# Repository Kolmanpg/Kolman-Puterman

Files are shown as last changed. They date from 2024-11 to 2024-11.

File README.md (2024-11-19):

# PCB Design Portfolio

Welcome to my portfolio of PCB design projects! This repository showcases my skills and experience in PCB design, focusing on projects done for my Formula SAE Electric Team, Nittany Motorsports!

## About Me
I am an Electrical Engineering student with a minor in Computer Engineering at Penn State University, experienced in PCB layout, circuit design, and testing. Apart from my work as a project manager for Nittany Motorsports, I am an Undergraduate Research Assistant. My research focuses on power delivery applications in the semiconductor packaging industry.

## Projects

### 1. **Megaboard Front**
- **Description:** This board is responsible for controlling key aspects of the race vehicle. It is built around an STM32F4 and contains various features that allow the vehicle to function as designed and adhere to all regulations.
- **Key Features:**
  - Custom power delivery architecture with multi-stage voltage regulation to ensure maximum efficiency.
  - Integration of high-speed components on the same board as sensitive analog circuits.
  - Integration of multiple safety circuits as required by the rulebook.
- **3D Rendering:**
Megaboard Front V3

### 2. **Megaboard Rear**
- **Description:** This board is responsible for controlling key aspects of the race vehicle. It is built around an STM32F4 and contains various features that allow the vehicle to function as designed and adhere to all regulations.
- **Key Features:**
  - Custom power delivery architecture with multi-stage voltage regulation to ensure maximum efficiency.
  - Integration of high-speed components on the same board as sensitive analog circuits.
  - Integration of both high-voltage and low-voltage circuits on the same board while ensuring necessary isolation.
  - Includes an ESP32 microcontroller utilized for Over-The-Air (OTA) software updates and telemetry.
- **3D Rendering:**
Megaboard Rear V3

### 3. **BMS Segment PCB (ADBMS6830B)**
- **Description:** Developed a Battery Management System (BMS) segment PCB centered around the ADBMS6830B. This PCB is custom-built to fit exactly on top of one of our high-voltage battery segments. It is designed to monitor and discharge all 16 cells on a segment and is built to endure high EMI and noise commonly found inside large high-voltage battery packs.
- **Key Features:**
  - High-precision cell voltage monitoring.
  - Dual isoSPI channels.
  - Stackup configured to minimize noise across the PCB.
- **3D Rendering:**
Segment PCB

## Skills Demonstrated
- Multi-layer PCB layout and design
- Integration of high-speed and high-power components
- Expertise in battery management systems and related ICs
- Prototyping and functional testing

## Repository Structure
Each folder of the repository contains:
- KiCad project files (schematics, layouts, and designs)
- Gerber files for PCB manufacturing
- Bill of Materials (BOM) for component sourcing

## Tools Used
- **PCB Design:** KiCad, Altium Designer
- **Simulations:** LTSPICE, MATLAB, Multisim
- **Prototyping:** Oscilloscopes, Logic Analyzers, Power Supplies, Arbitrary Waveform Generators

## Get in Touch
Feel free to reach out to me with any questions or collaboration ideas!

- Email: Kolmanpg@gmail.com
- [LinkedIn](https://www.linkedin.com/in/Kolmanp)

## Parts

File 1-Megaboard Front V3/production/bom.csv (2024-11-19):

Designator | Footprint | Quantity | Value | LCSC Part #
+VIN1, +VOUT1, -VIN1, -VOUT1, TP1, TP10, TP11, TP12, TP13, TP14, TP15, TP16, TP17, TP18, TP19, TP2, TP20, TP21, TP22, TP23, TP24, TP25, TP26, TP27, TP28, TP29, TP3, TP30, TP31, TP32, TP33, TP34, TP35, TP37, TP38, TP39, TP4, TP41, TP42, TP43, TP44, TP46, TP47, TP5, TP6, TP8, TP9 | TestPoint_Pad_D1.0mm | 47 | ~ | DNP
C1, C10, C11, C12, C22, C23, C25, C27, C29, C3, C30, C31, C33, C37, C4, C41, C46, C49, C5, C50, C51, C6, C7, C8, C9 | 0805 | 25 | 0.1u | C49678
C13, C14 | 0805 | 2 | DNP | DNP
C15, C16, C17, C18, C19, C20, C34, C35, C44, C52, C53, C54 | 0805 | 12 | 1u | C28323
C2 | 0805 | 1 | 4.7u | C1779
C21, C26 | 0805 | 2 | _MHz | DNP
C24, C28 | 0805 | 2 | C_Small | DNP
C32, C48 | 0805 | 2 | 1n | C46653
C36, C47 | 0805 | 2 | 10u | C15850
C38, C39, C42, C43 | CP_EIA-3216-18_Kemet-A | 4 | 10u | C7171
C40 | 0805 | 1 | 10n | C1710
C45 | PCAP_TPB_D4_PAN | 1 | 220u | C242173
D1, D2, D3, D4, D5, D6, D7, D8 | SOD323_F_ | 8 | 1PS76SB17-115 | C551398
D10 | SOT-23 | 1 | NUP2105L | C2890118
D11 | D_SMA | 1 | SS34 | C8678
D12, D13, D16, D9 | 0805 | 4 | NCD0805R1 | C84256
D14 | D_SMA_Handsoldering | 1 | 1N4004 | C727080
D15 | 0805 | 1 | LED | C2297
D17 | HPZRC14X | 1 | HPZR-C14X | DNP
H1, H2, H3, H4 | MountingHole_3.2mm_M3 | 4 | MountingHole | DNP
J1 | PinHeader_2x03_P2.54mm_Vertical | 1 | Conn_01x06 | DNP
J2 | CONN_500762-1001_MOL | 1 | 5007621001 | DNP
JP1 | SolderJumper-2_P1.3mm_Open_RoundedPad1.0x1.5mm | 1 | NC | DNP
JP2, JP3, JP4 | SolderJumper-3_P1.3mm_Open_RoundedPad1.0x1.5mm | 3 | SolderJumper_3_Open
K1 | RELAY_DSP2A_PAN | 1 | DSP2A-DC12V | DNP
L1 | IND_CDRH104_SUM | 1 | 15uH | C225048
Q1, Q2, Q3 | SOT-23 | 3 | MMBF170 | C151058
Q4 | SOT-23 | 1 | MMFTP2319 | DNP
R1 | 0805 | 1 | 2k2 | C17520
R10, R3, R36, R4, R42, R48, R49, R50, R55, R57, R61, R65, R66, R68, R69, R7, R8, R85, R86, R9 | 0805 | 20 | 10k | C17414
R11, R12, R15, R16, R17, R18, R64 | 0805 | 7 | 3k8 | C228799
R13, R14, R46, R47, R82, R84 | 0805 | 6 | 9.7k | C374689
R19, R53 | 0805 | 2 | 200 | C17540
R2, R59, R60, R71, R87 | 0805 | 5 | 100k | C149504
R20, R21, R28 | 0805 | 3 | 0R | C17477
R22, R23, R24, R25, R26, R27 | 0805 | 6 | 82 | C17841
R29, R41, R56 | 0805 | 3 | 15k | C17475
R30 | 0805 | 1 | 66
R31 | 0805 | 1 | 14k | C17464
R32 | 0805 | 1 | 453
R33 | 0805 | 1 | 120 | C17437
R34, R35 | 0805 | 2 | 1M | C17514
R37, R38, R51, R77 | 0805 | 4 | 82k | C17840
R39, R40, R52, R78 | 0805 | 4 | 18k | C17506
R43, R58 | 0805 | 2 | 47k | C17713
R44, R45, R5, R6, R79, R83 | 0805 | 6 | 5k | C2828700
R54 | 0805 | 1 | 68k | C17801
R62 | 0805 | 1 | 3.24k | C4194377
R63 | 0805 | 1 | 330R | C17630
R67 | 0805 | 1 | 2k | C17604
R70, R73, R74 | 0805 | 3 | 1k | C17513
R72 | 0805 | 1 | 300 | C17617
R75, R76, R80, R81 | 0805 | 4 | DNP | C865361
RV1, RV2 | Potentiometer_Bourns_3296W_Vertical | 2 | 1k
RV3, RV4 | Potentiometer_Bourns_3296W_Vertical | 2 | 100k
SW1, SW2 | SW_Push_1P1T_XKB_TS-1187A | 2 | SW_MEC_5G | C318884
U1 | LQFP-64_10x10mm_P0.5mm | 1 | STM32F446RETx | C69336
U10 | TI_SO-PowerPAD-8_ThermalVias | 1 | TPS5431DDA | C9864
U11 | SOIC-14_3.9x8.7mm_P1.27mm | 1 | 74HC14 | C5605
U12, U13, U14, U17 | SOIC-8_3.9x4.9mm_P1.27mm | 4 | LM393 | C32901
U15 | SOT95P280X125-5N | 1 | BU4S71G2-TR | C2837802
U16 | SOIC127P600X175-14N | 1 | HEF4081BT,653 | C148318
U2, U3, U4, U5, U8 | SOIC-8_3.9x4.9mm_P1.27mm | 5 | LM358 | C9418
U6 | SOIC-16_3.9x9.9mm_P1.27mm | 1 | MAX3232 | C18261
U7 | SOIC-8_3.9x4.9mm_P1.27mm | 1 | SN65HVD230 | C12084
U9 | SOT-223-3_TabPin2 | 1 | AMS1117-3.3 | C6186
Y1 | Crystal_SMD_3225-4Pin_3.2x2.5mm_HandSoldering | 1 | Crystal_GND24_Small
Y2 | Crystal_SMD_3215-2Pin_3.2x1.5mm | 1 | Crystal_GND23_Small | DNP

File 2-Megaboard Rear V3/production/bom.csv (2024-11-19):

Designator | Footprint | Quantity | Value | LCSC Part #
C1, C10, C11, C12, C13, C14, C15, C16, C17, C2, C20, C25, C26, C28, C3, C30, C31, C38, C4, C43, C6, C7, C8, C9 | 0805 | 24 | 0.1u | C28233
C18, C19, C36, C37, C39, C40, C46, C47 | CP_EIA-3216-18_Kemet-A | 8 | 10u | C7171
C21, C22 | 0805 | 2 | 20p | C1798
C23, C24 | 0805 | 2 | 22p | C1804
C27, C29 | 0805 | 2 | 2.2n | C28260
C32, C35 | 0805 | 2 | 1u | DNP
C33, C49 | 0805 | 2 | 10n | C1710
C34, C48 | 0805 | 2 | 10u | C15850
C41, C42, C44, C45, C51 | 0805 | 5 | 1u | C28323
C5 | 0805 | 1 | 4.7u | C1779
C50 | PCAP_TPB_D4_PAN | 1 | 220u | C242173
C52 | 0805 | 1 | DNP | DNP
D1, D13 | SOT-23 | 2 | NUP2105L | C284104
D10, D11, D12, D6, D7, D9 | D_MiniMELF | 6 | ZMM3V3-M | DNP
D14, D15, D16, D17, D19, D2, D4 | 0805 | 7 | NCD0805R1 | C84256
D18 | D_SMA | 1 | SS34 | C8678
D3 | D_SMA | 1 | US1M | C412437
D5 | D_MiniMELF | 1 | BZV55C15 | C545332
D8 | 0805 | 1 | KT-0805G | C2297
H1, H2, H3, H4 | MountingHole_3.2mm_M3 | 4 | MountingHole | DNP
HV+1, HV-1, TP1, TP36, TP37 | TestPoint_Pad_D1.0mm | 5 | HIL_TSAL_HV_GND | DNP
J1 | CONN_500762-1001_MOL | 1 | 5007621001 | DNP
J2 | microSD_HC_Molex_104031-0811 | 1 | Micro_SD_Card_Det | C585350
J3 | PinHeader_1x03_P2.54mm_Vertical | 1 | Conn_01x03
J4 | PinHeader_2x03_P2.54mm_Vertical | 1 | Conn_02x03_Odd_Even
J5 | PinHeader_1x04_P2.54mm_Vertical | 1 | Conn_01x04 | DNP
JP1, JP2 | SolderJumper-2_P1.3mm_Open_RoundedPad1.0x1.5mm | 2 | NC | DNP
JP5, JP6 | SolderJumper-2_P1.3mm_Open_RoundedPad1.0x1.5mm | 2 | Jumper_2_Open
L1 | IND_CDRH104_SUM | 1 | 15uH | C225048
Q1, Q2, Q3, Q4 | SOT-23 | 4 | AO3400A | C20917
Q5, Q6, Q7, Q8, Q9 | SOT-23 | 5 | MMBF170 | C20917
R1, R10, R15, R16, R3, R35, R42, R44, R6, R63, R65, R67 | 0805 | 12 | 10k | C17414
R11, R20, R7, R8 | 0805 | 4 | 0R | C17477
R12, R5 | 0805 | 2 | 120 | C17437
R13, R17, R62, R9 | 0805 | 4 | 200 | C17540
R14, R25, R43 | 0805 | 3 | 2k2 | C17520
R18, R19 | 0805 | 2 | 4k7 | C17673
R2, R4 | 0805 | 2 | 4.7k | C17673
R21, R22, R23, R24, R27, R28, R29, R30 | 0805 | 8 | 300k | C149504
R26, R32 | 0805 | 2 | 1k | C17513
R31 | 0805 | 1 | 18k | C17506
R33 | 2512 | 1 | 0.01R | C149504
R34 | 0805 | 1 | 1k2 | C17379
R36, R45, R52, R55, R58, R61 | 0805 | 6 | 9k1 | C17855
R37 | 0805 | 1 | 22k | C17560
R38 | 0805 | 1 | 51k | C17737
R40, R46 | 0805 | 2 | 82 | C17477
R41, R47, R49, R54, R57, R60 | 0805 | 6 | 3k6 | C18359
R48 | 0805 | 1 | 1k3 | C17414
R50, R53, R56, R59 | 0805 | 4 | 82 | C23255
R51 | 0805 | 1 | 47 | C17714
R64 | 0805 | 1 | 3.24k | C4194377
R66 | 0805 | 1 | 330R | C17630
SW1, SW2, SW3, SW4 | SW_Push_1P1T_XKB_TS-1187A | 4 | SW_MEC_5G | C318884
TP10, TP11, TP12, TP13, TP14, TP15, TP16, TP17, TP18, TP19, TP20, TP21, TP22, TP23, TP24, TP25, TP26, TP27, TP28, TP29, TP30, TP31, TP32, TP33, TP34, TP35, TP38, TP39, TP40, TP5, TP6, TP7, TP8, TP9 | TestPoint_Pad_D1.0mm | 34 | ~ | DNP
TP2 | TestPoint_Pad_D1.0mm | 1 | HIL_IN_TSAL | DNP
TP3 | TestPoint_Pad_D1.0mm | 1 | DIS | DNP
TP4 | TestPoint_Pad_D1.0mm | 1 | THR | DNP
U1, U5 | SOIC-8_3.9x4.9mm_P1.27mm | 2 | SN65HVD230 | C12084
U10, U15, U17 | SOIC-8_3.9x4.9mm_P1.27mm | 3 | LM358 | C7950
U11 | SOIC-8_3.9x4.9mm_P1.27mm | 1 | NE555DR | C7593
U12 | SOP-4_3.8x4.1mm_P2.54mm | 1 | EL357NC | C29981
U13 | D24V150F12 | 1 | DV24V150F12 | DNP
U14, U16 | SOT-223-3_TabPin2 | 2 | AMS1117-3.3
U18 | TI_SO-PowerPAD-8_ThermalVias | 1 | TPS5431DDA
U2 | SOT-23-6 | 1 | TMP101 | C388175
U3 | ESP32-WROOM-32 | 1 | ESP32-WROOM-32 | C529581
U4 | LQFP-64_10x10mm_P0.5mm | 1 | STM32F446RETx | C69336
U6 | TSSOP-16_4.4x5mm_P0.65mm | 1 | MAX3232 | C13482
U7 | Converter_DCDC_TRACO_TMR-xxxx_THT | 1 | TMR-1212 | DNP
U8 | InvenSense_QFN-24_4x4mm_P0.5mm | 1 | MPU-6050 | C24112
U9 | SOIC-8_3.9x4.9mm_P1.27mm | 1 | LM393 | C7955
Y1 | Crystal_SMD_3225-4Pin_3.2x2.5mm_HandSoldering | 1 | 9p | C13738
Y2 | Crystal_SMD_3215-2Pin_3.2x1.5mm | 1 | 12p5 | C32346

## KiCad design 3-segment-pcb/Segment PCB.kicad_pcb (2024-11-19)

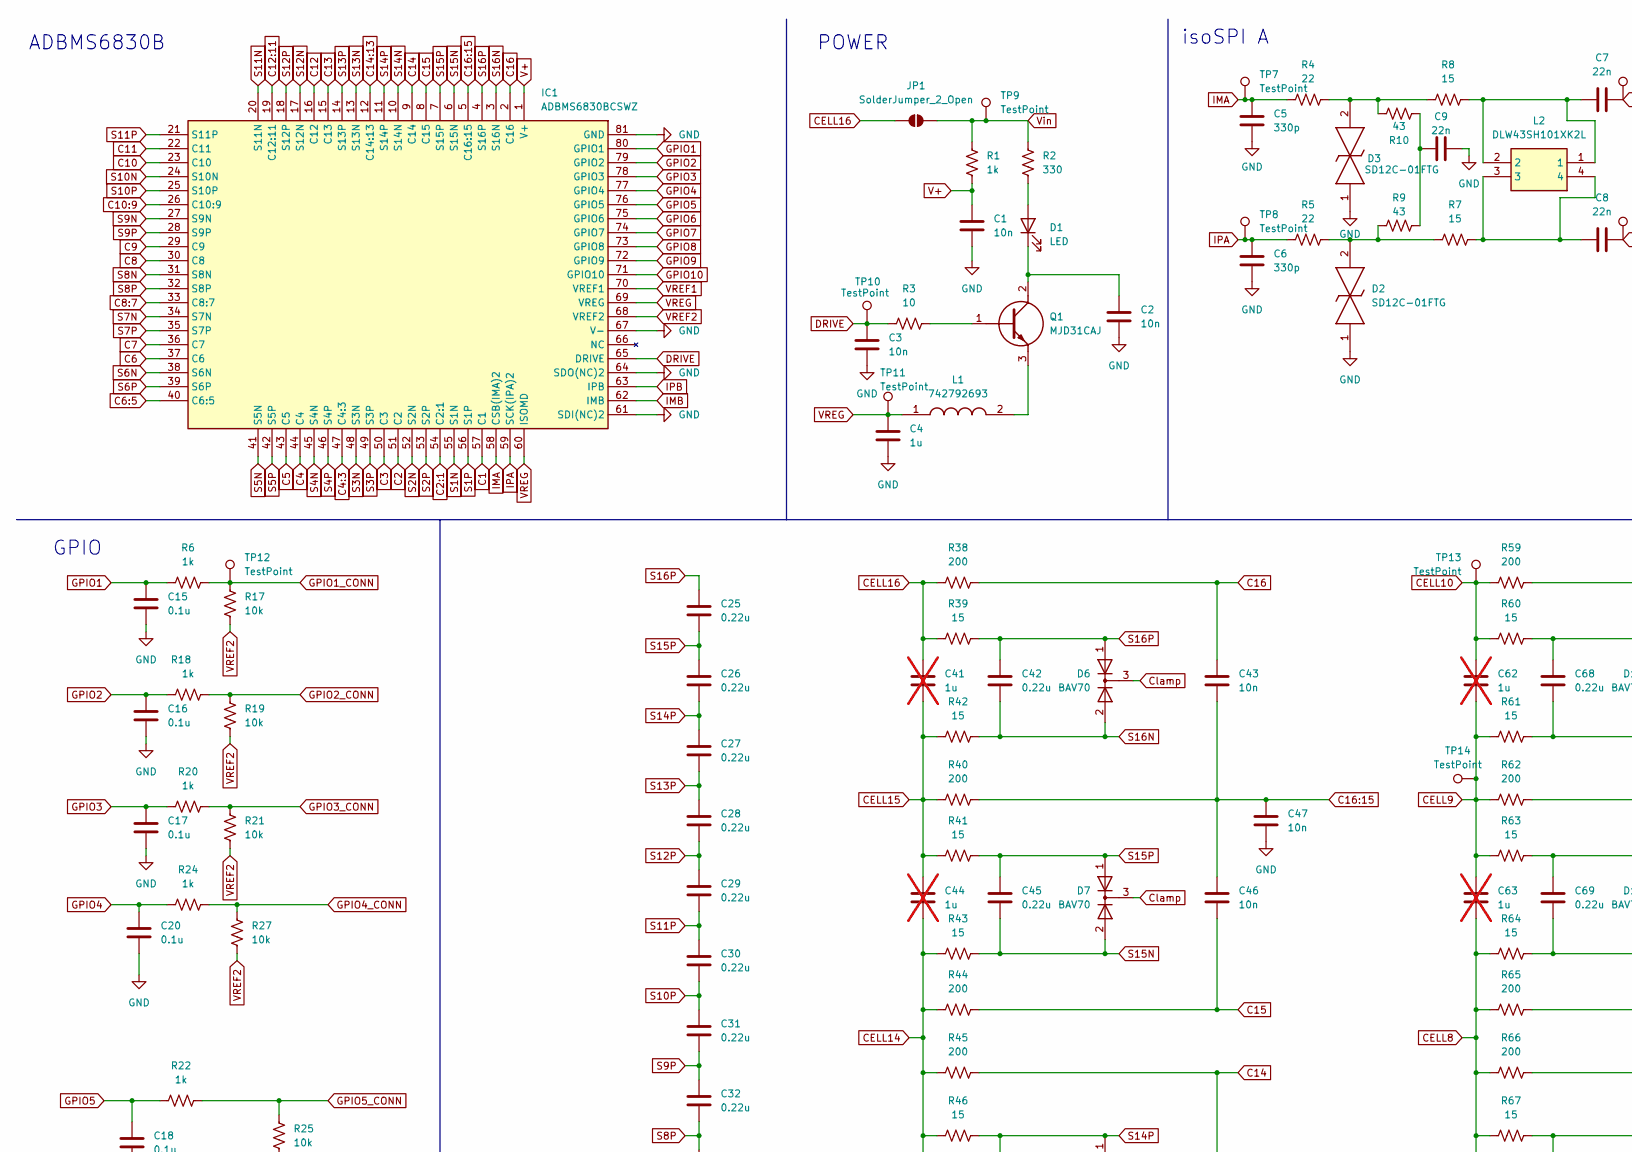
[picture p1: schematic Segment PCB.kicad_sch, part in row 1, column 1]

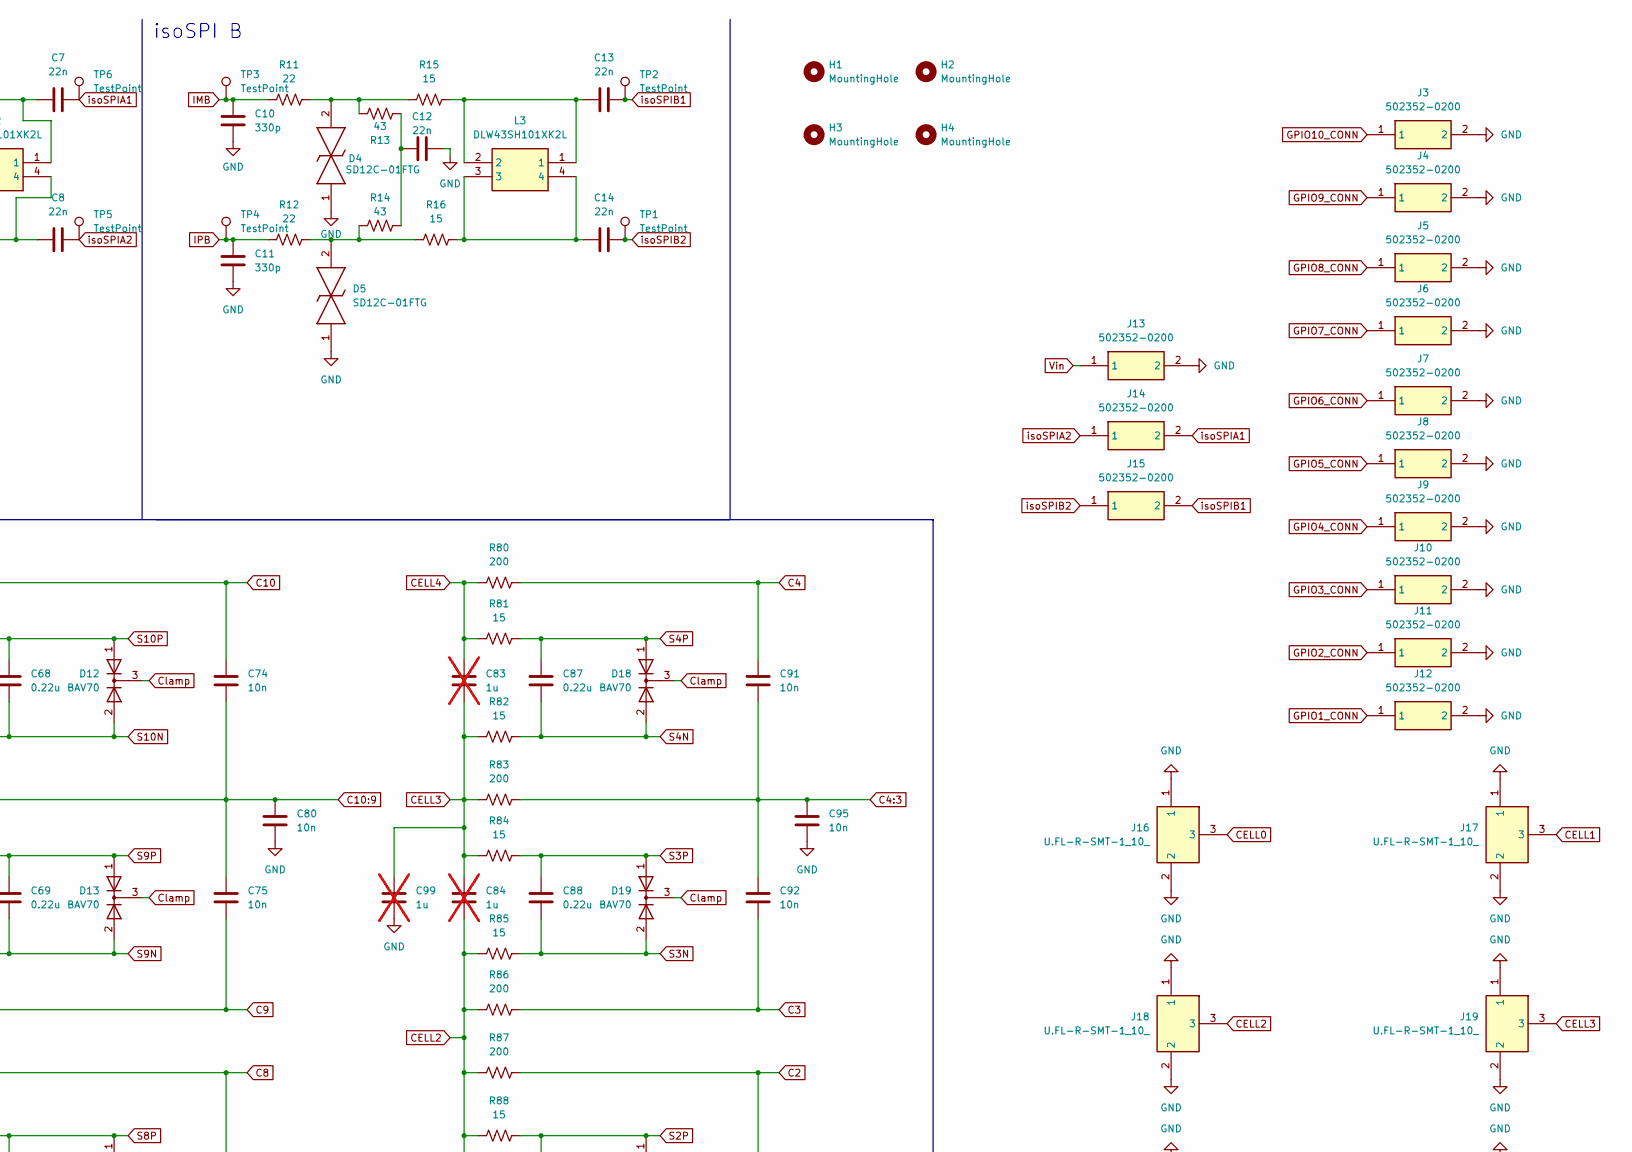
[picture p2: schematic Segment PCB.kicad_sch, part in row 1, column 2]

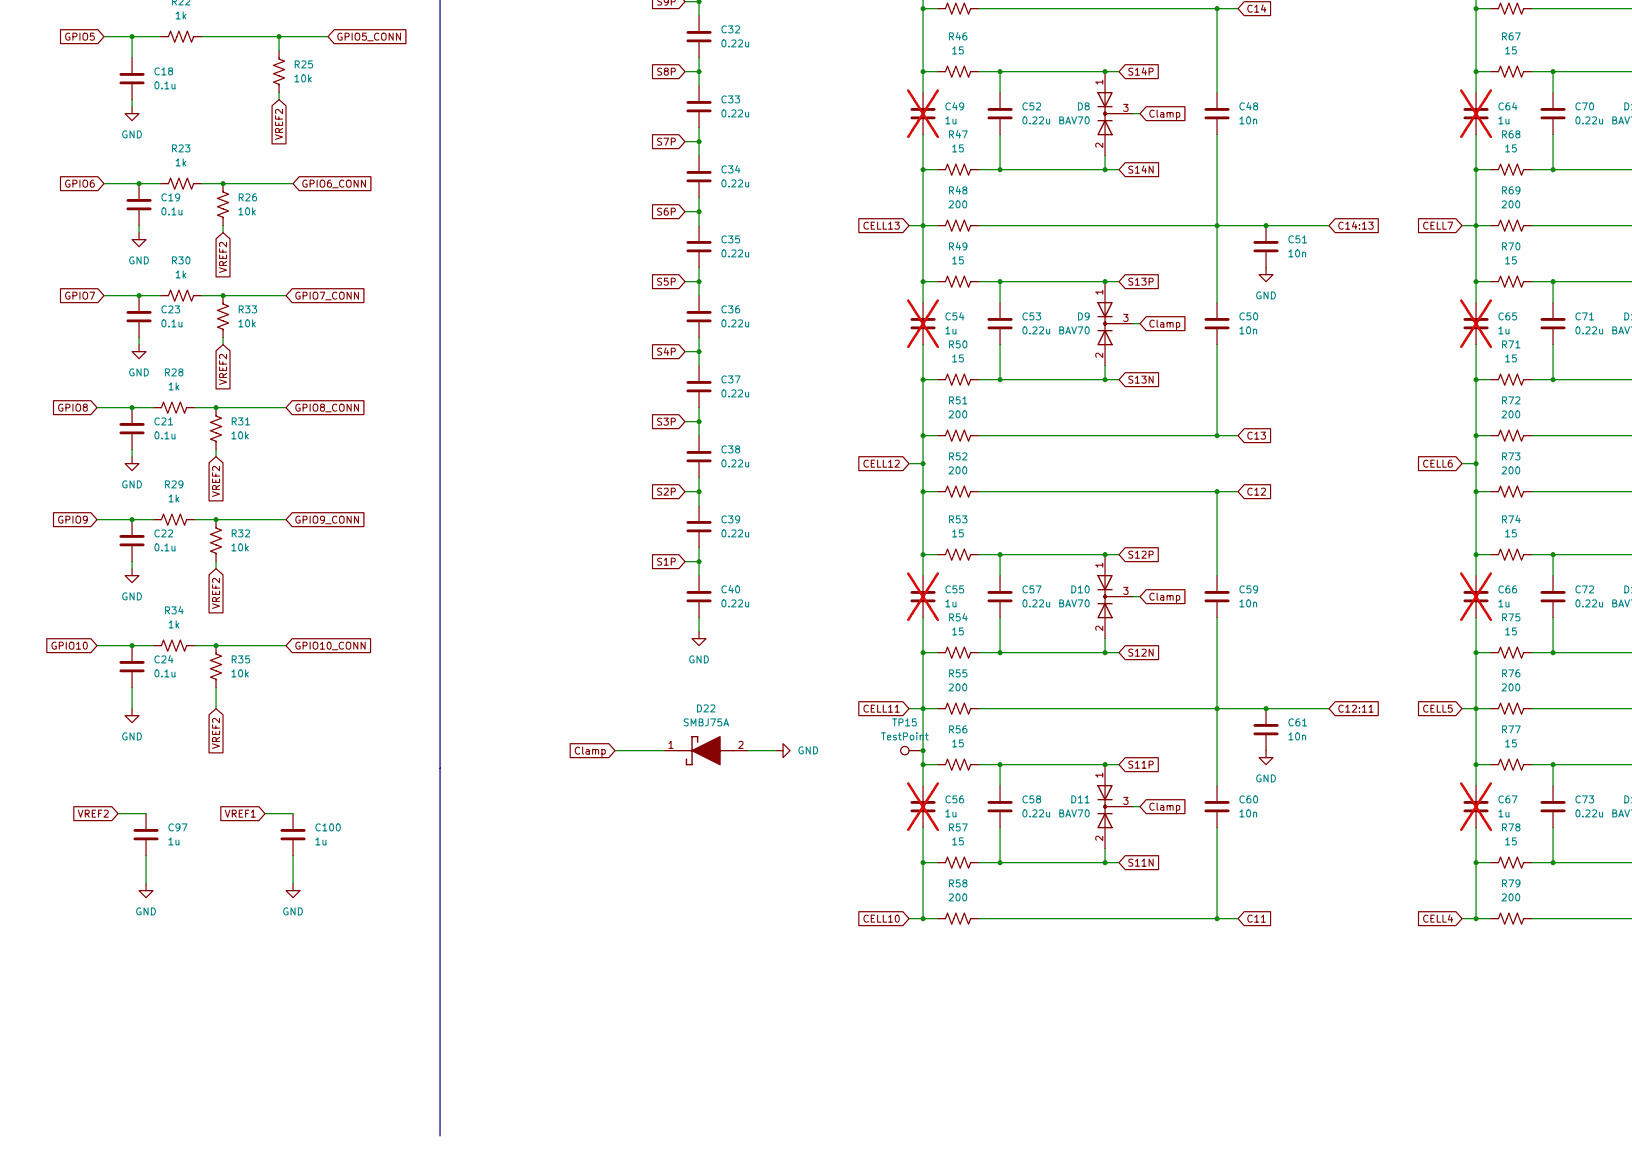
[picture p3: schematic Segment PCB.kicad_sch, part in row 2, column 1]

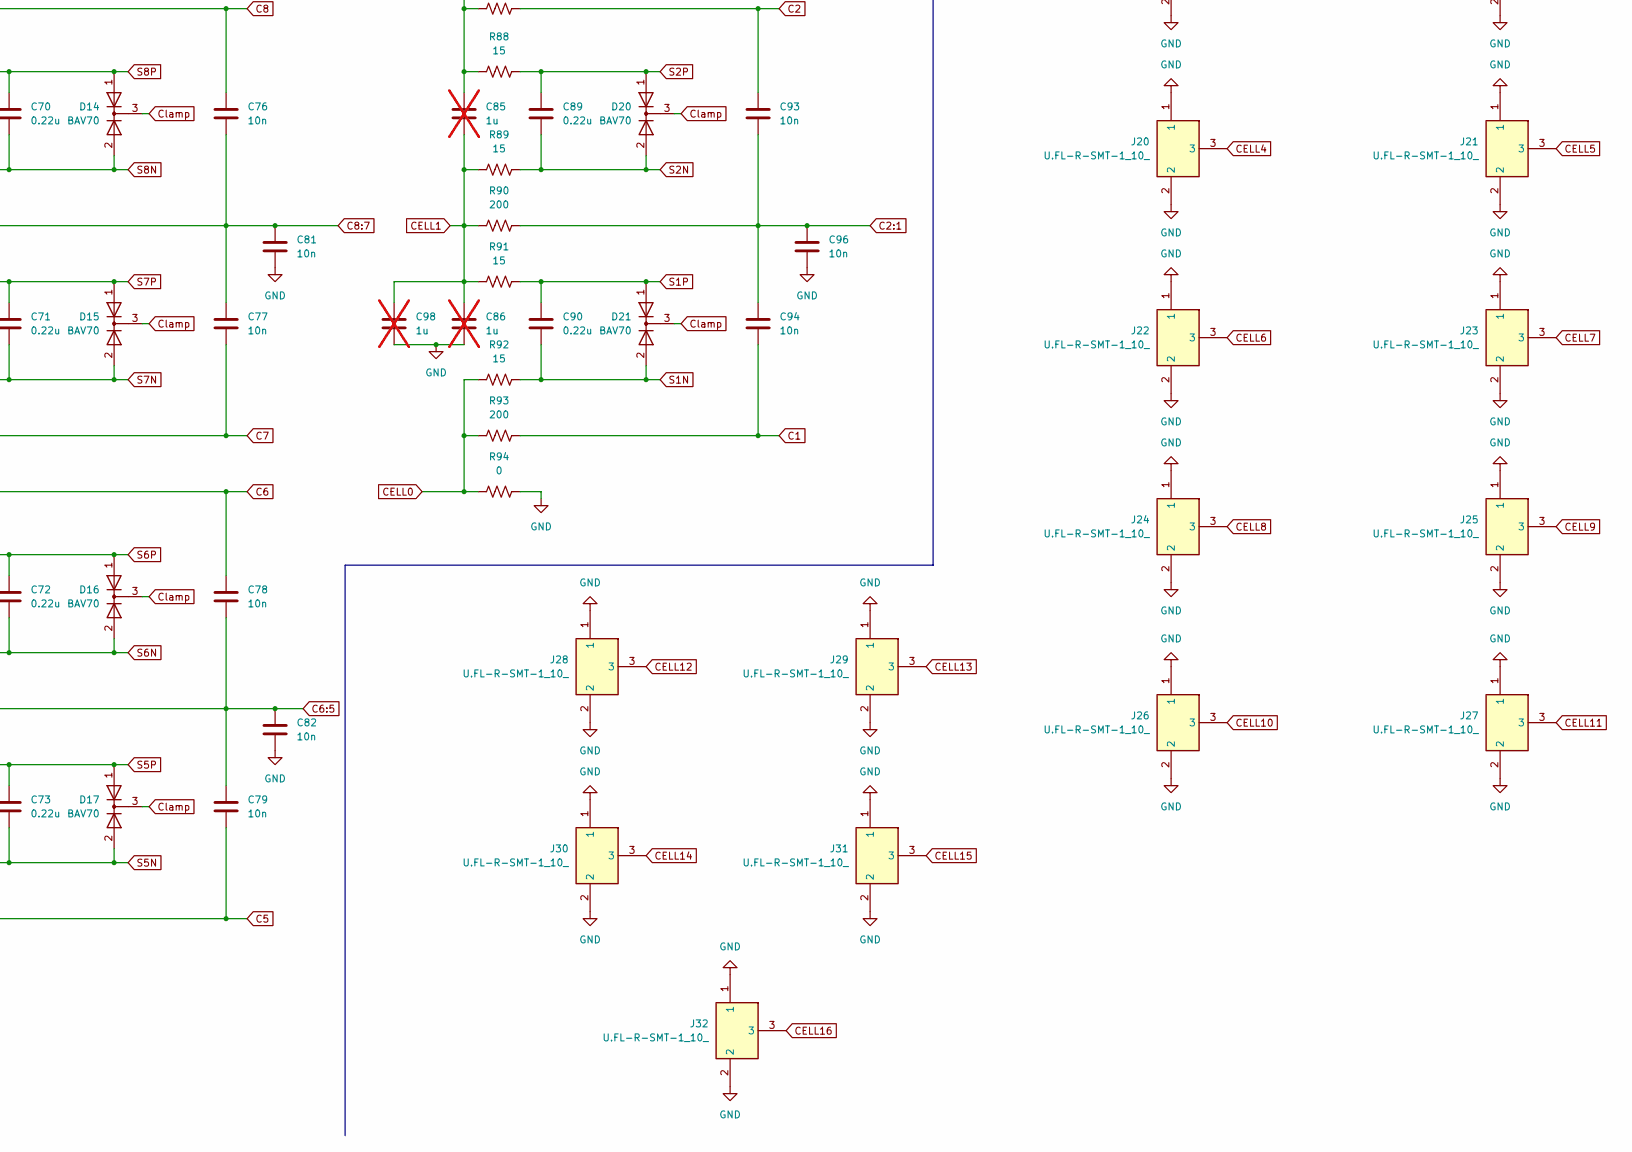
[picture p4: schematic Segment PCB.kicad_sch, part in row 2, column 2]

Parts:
C1, C2, C3, C43, C46, C47, C48, C50, C51, C59, C60, C61, C74, C75, C76, C77, C78, C79, C80, C81, C82, C91, C92, C93, C94, C95, C96: 10n; C_0805_2012Metric_Pad1.18x1.45mm_HandSolder; Manufacturer_Part_Number CL21B103KBANNNC; JLCPCB C1710
C4, C97, C100: 1u; C_0805_2012Metric_Pad1.18x1.45mm_HandSolder; Manufacturer_Part_Number CL21B105KBFNNNE; JLCPCB C28323
C5, C6, C10, C11: 330p; C_0805_2012Metric_Pad1.18x1.45mm_HandSolder
C7, C8, C9, C12, C13, C14: 22n; C_0805_2012Metric_Pad1.18x1.45mm_HandSolder; Manufacturer_Part_Number CL21B223KBANNNC; JLCPCB C1729
C15, C16, C17, C18, C19, C20, C21, C22, C23, C24: 0.1u; C_0805_2012Metric_Pad1.18x1.45mm_HandSolder; Manufacturer_Part_Number CL21B104KCFNNNE; JLCPCB C28233
C25, C26, C27, C28, C29, C30, C31, C32, C33, C34, C35, C36, C37, C38, C39, C40, C42, C45, C52, C53, C57, C58, C68, C69, C70, C71, C72, C73, C87, C88, C89, C90: 0.22u; C_0805_2012Metric_Pad1.18x1.45mm_HandSolder; Manufacturer_Part_Number CL21B224KBFNNNE; JLCPCB C5378
C41, C44, C49, C54, C55, C56, C62, C63, C64, C65, C66, C67, C83, C84, C85, C86, C98, C99: 1u; C_0805_2012Metric_Pad1.18x1.45mm_HandSolder; Manufacturer_Part_Number CL21B105KBFNNNE; JLCPCB C28323; not fitted
D1: LED; LED_0805_2012Metric_Pad1.15x1.40mm_HandSolder; Manufacturer_Part_Number KT-0805G; JLCPCB C2297
D2, D3, D4, D5: SD12C-01FTG; SOD2613X114N; Mouser Part Number 576-SD12C-01FTG
D6, D7, D8, D9, D10, D11, D12, D13, D14, D15, D16, D17, D18, D19, D20, D21: BAV70; SOT-23; Manufacturer_Part_Number BAV70; JLCPCB C68978
D22: SMBJ75A; Mouser Part Number 750-CDBB3200-HF
H1, H2, H3, H4: MountingHole; MountingHole_3mm
IC1: ADBMS6830BCSWZ; QFP50P1400X1400X160-81N; Mouser Part Number 584-ADBMS6830BCSWZ
J3, J4, J5, J6, J7, J8, J9, J10, J11, J12, J13, J14, J15: 502352-0200; 5023520200; Mouser Part Number 538-502352-0200
J16, J17, J18, J19, J20, J21, J22, J23, J24, J25, J26, J27, J28, J29, J30, J31, J32: U.FL-R-SMT-1_10_; Mouser Part Number 798-U.FL-R-SMT-110
JP1: SolderJumper_2_Open; SolderJumper-2_P1.3mm_Open_RoundedPad1.0x1.5mm
L1: 742792693; INDC1608X100N; Mouser Part Number 710-742792693
L2, L3: DLW43SH101XK2L; Mouser Part Number 81-DLW43SH101XK2L
Q1: MJD31CAJ; Mouser Part Number 771-MJD31CAJ
R1, R6, R18, R20, R22, R23, R24, R28, R29, R30, R34: 1k; R_0805_2012Metric_Pad1.20x1.40mm_HandSolder; Manufacturer_Part_Number 0805W8F1001T5E; JLCPCB C17513
R2: 330; R_0805_2012Metric_Pad1.20x1.40mm_HandSolder; Manufacturer_Part_Number 0805W8F3300T5E; JLCPCB C17630
R3: 10; R_0805_2012Metric_Pad1.20x1.40mm_HandSolder; Manufacturer_Part_Number 0805W8F100JT5E; JLCPCB C17415
R4, R5, R11, R12: 22; R_0805_2012Metric_Pad1.20x1.40mm_HandSolder; Manufacturer_Part_Number 0805W8F220JT5E; JLCPCB C17561
R7, R8, R15, R16: 15; R_0805_2012Metric_Pad1.20x1.40mm_HandSolder
R9, R10, R13, R14: 43; R_0805_2012Metric_Pad1.20x1.40mm_HandSolder
R17, R19, R21, R25, R26, R27, R31, R32, R33, R35: 10k; R_0805_2012Metric_Pad1.20x1.40mm_HandSolder; Manufacturer_Part_Number 0805W8F1002T5E; JLCPCB C17414
R38, R40, R44, R45, R48, R51, R52, R55, R58, R59, R62, R65, R66, R69, R72, R73, R76, R79, R80, R83, R86, R87, R90, R93: 200; R_0805_2012Metric_Pad1.20x1.40mm_HandSolder; Manufacturer_Part_Number 0805W8F2000T5E; JLCPCB C17540
R39, R41, R42, R43, R46, R47, R49, R50, R53, R54, R56, R57, R60, R61, R63, R64, R67, R68, R70, R71, R74, R75, R77, R78, R81, R82, R84, R85, R88, R89, R91, R92: 15; RESC6432X65N; Manufacturer_Part_Number 352115RFT
R94: 0; R_0805_2012Metric_Pad1.20x1.40mm_HandSolder; Manufacturer_Part_Number 0805W8F0000T5E; JLCPCB C17477
TP1, TP2, TP3, TP4, TP5, TP6, TP7, TP8, TP9, TP10, TP11, TP12, TP13, TP14, TP15: TestPoint; TestPoint_Pad_D1.0mm

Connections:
C1: C94.2, IC1.57 (C1), R93.2
C2: C93.1, IC1.51 (C2), R87.2
C2:1: C93.2, C94.1, C96.1, IC1.54 (C2:1), R90.2
C3: C92.2, IC1.50 (C3), R86.2
C4: C91.1, IC1.44 (C4), R80.2
C4:3: C91.2, C92.1, C95.1, IC1.47 (C4:3), R83.2
C5: C79.2, IC1.43 (C5), R79.2
C6: C78.1, IC1.37 (C6), R73.2
C6:5: C78.2, C79.1, C82.1, IC1.40 (C6:5), R76.2
C7: C77.2, IC1.36 (C7), R72.2
C8: C76.1, IC1.30 (C8), R66.2
C8:7: C76.2, C77.1, C81.1, IC1.33 (C8:7), R69.2
C9: C75.2, IC1.29 (C9), R65.2
C10: C74.1, IC1.23 (C10), R59.2
C10:9: C74.2, C75.1, C80.1, IC1.26 (C10:9), R62.2
C11: C60.2, IC1.22 (C11), R58.2
C12: C59.1, IC1.16 (C12), R52.2
C12:11: C59.2, C60.1, C61.1, IC1.19 (C12:11), R55.2
C13: C50.2, IC1.15 (C13), R51.2
C14: C48.1, IC1.9 (C14), R45.2
C14:13: C48.2, C50.1, C51.1, IC1.12 (C14:13), R48.2
C15: C46.2, IC1.8 (C15), R44.2
C16: C43.1, IC1.2 (C16), R38.2
C16:15: C43.2, C46.1, C47.1, IC1.5 (C16:15), R40.2
CELL0: J16.3, R92.1, R93.1, R94.1
CELL1: C85.2, C86.1, C98.1, J17.3, R89.1, R90.1, R91.1
CELL2: C84.2, C85.1, J18.3, R85.1, R86.1, R87.1, R88.1
CELL3: C83.2, C84.1, C99.1, J19.3, R82.1, R83.1, R84.1
CELL4: C67.2, C83.1, J20.3, R78.1, R79.1, R80.1, R81.1
CELL5: C66.2, C67.1, J21.3, R75.1, R76.1, R77.1
CELL6: C65.2, C66.1, J22.3, R71.1, R72.1, R73.1, R74.1
CELL7: C64.2, C65.1, J23.3, R68.1, R69.1, R70.1
CELL8: C63.2, C64.1, J24.3, R64.1, R65.1, R66.1, R67.1
CELL9: C62.2, C63.1, J25.3, R61.1, R62.1, R63.1, TP14.1
CELL10: C56.2, C62.1, J26.3, R57.1, R58.1, R59.1, R60.1, TP13.1
CELL11: C55.2, C56.1, J27.3, R54.1, R55.1, R56.1, TP15.1
CELL12: C54.2, C55.1, J28.3, R50.1, R51.1, R52.1, R53.1
CELL13: C49.2, C54.1, J29.3, R47.1, R48.1, R49.1
CELL14: C44.2, C49.1, J30.3, R43.1, R44.1, R45.1, R46.1
CELL15: C41.2, C44.1, J31.3, R40.1, R41.1, R42.1
CELL16: C41.1, J32.3, JP1.1 (A), R38.1, R39.1
Clamp: D6.3 (K), D7.3 (K), D8.3 (K), D9.3 (K), D10.3 (K), D11.3 (K), D12.3 (K), D13.3 (K), D14.3 (K), D15.3 (K), D16.3 (K), D17.3 (K), D18.3 (K), D19.3 (K), D20.3 (K), D21.3 (K), D22.1 (K)
DRIVE: C3.1, IC1.65 (DRIVE), R3.1, TP10.1
GND: C1.2, C2.2, C3.2, C4.2, C5.2, C6.2, C9.2, C10.2, C11.2, C12.2, C15.2, C16.2, C17.2, C18.2, C19.2, C20.2, C21.2, C22.2, C23.2, C24.2, C40.2, C47.2, C51.2, C61.2, C80.2, C81.2, C82.2, C86.2, C95.2, C96.2, C97.2, C98.2, C99.2, C100.2, D2.1, D3.1, D4.1, D5.1, D22.2 (A), IC1.61 (SDI(NC)2), IC1.64 (SDO(NC)2), IC1.67 (V-), IC1.81 (GND), J3.2, J4.2, J5.2, J6.2, J7.2, J8.2, J9.2, J10.2, J11.2, J12.2, J13.2, J16.1, J16.2, J17.1, J17.2, J18.1, J18.2, J19.1, J19.2, J20.1, J20.2, J21.1, J21.2, J22.1, J22.2, J23.1, J23.2, J24.1, J24.2, J25.1, J25.2, J26.1, J26.2, J27.1, J27.2, J28.1, J28.2, J29.1, J29.2, J30.1, J30.2, J31.1, J31.2, J32.1, J32.2, R94.2
GPIO1: C15.1, IC1.80 (GPIO1), R6.1
GPIO1_CONN: J12.1, R6.2, R17.2, TP12.1
GPIO2: C16.1, IC1.79 (GPIO2), R18.1
GPIO2_CONN: J11.1, R18.2, R19.2
GPIO3: C17.1, IC1.78 (GPIO3), R20.1
GPIO3_CONN: J10.1, R20.2, R21.2
GPIO4: C20.1, IC1.77 (GPIO4), R24.1
GPIO4_CONN: J9.1, R24.2, R27.2
GPIO5: C18.1, IC1.76 (GPIO5), R22.1
GPIO5_CONN: J8.1, R22.2, R25.2
GPIO6: C19.1, IC1.75 (GPIO6), R23.1
GPIO6_CONN: J7.1, R23.2, R26.2
GPIO7: C23.1, IC1.74 (GPIO7), R30.1
GPIO7_CONN: J6.1, R30.2, R33.2
GPIO8: C21.1, IC1.73 (GPIO8), R28.1
GPIO8_CONN: J5.1, R28.2, R31.2
GPIO9: C22.1, IC1.72 (GPIO9), R29.1
GPIO9_CONN: J4.1, R29.2, R32.2
GPIO10: C24.1, IC1.71 (GPIO10), R34.1
GPIO10_CONN: J3.1, R34.2, R35.2
IMA: C5.1, IC1.58 (CSB(IMA)2), R4.1, TP7.1
IMB: C10.1, IC1.62 (IMB), R11.1, TP3.1
IPA: C6.1, IC1.59 (SCK(IPA)2), R5.1, TP8.1
IPB: C11.1, IC1.63 (IPB), R12.1, TP4.1
unnamed: C7.1, L2.1, L2.2, R8.2
unnamed: C8.1, L2.3, L2.4, R7.2
unnamed: C9.1, R9.2, R10.1
unnamed: C12.1, R13.1, R14.2
unnamed: C13.1, L3.1, L3.2, R15.2
unnamed: C14.1, L3.3, L3.4, R16.2
unnamed: D1.2 (A), R2.2
unnamed: C2.1, D1.1 (K), Q1.2 (C)
unnamed: D2.2, R5.2, R7.1, R9.1
unnamed: D3.2, R4.2, R8.1, R10.2
unnamed: D4.2, R11.2, R13.2, R15.1
unnamed: D5.2, R12.2, R14.1, R16.1
unnamed: Q1.1 (B), R3.2
unnamed: L1.2, Q1.3 (E)
S1N: C90.2, D21.2 (A), IC1.55 (S1N), R92.2
S1P: C39.2, C40.1, C90.1, D21.1 (A), IC1.56 (S1P), R91.2
S2N: C89.2, D20.2 (A), IC1.52 (S2N), R89.2
S2P: C38.2, C39.1, C89.1, D20.1 (A), IC1.53 (S2P), R88.2
S3N: C88.2, D19.2 (A), IC1.48 (S3N), R85.2
S3P: C37.2, C38.1, C88.1, D19.1 (A), IC1.49 (S3P), R84.2
S4N: C87.2, D18.2 (A), IC1.45 (S4N), R82.2
S4P: C36.2, C37.1, C87.1, D18.1 (A), IC1.46 (S4P), R81.2
S5N: C73.2, D17.2 (A), IC1.41 (S5N), R78.2
S5P: C35.2, C36.1, C73.1, D17.1 (A), IC1.42 (S5P), R77.2
S6N: C72.2, D16.2 (A), IC1.38 (S6N), R75.2
S6P: C34.2, C35.1, C72.1, D16.1 (A), IC1.39 (S6P), R74.2
S7N: C71.2, D15.2 (A), IC1.34 (S7N), R71.2
S7P: C33.2, C34.1, C71.1, D15.1 (A), IC1.35 (S7P), R70.2
S8N: C70.2, D14.2 (A), IC1.31 (S8N), R68.2
S8P: C32.2, C33.1, C70.1, D14.1 (A), IC1.32 (S8P), R67.2
S9N: C69.2, D13.2 (A), IC1.27 (S9N), R64.2
S9P: C31.2, C32.1, C69.1, D13.1 (A), IC1.28 (S9P), R63.2
S10N: C68.2, D12.2 (A), IC1.24 (S10N), R61.2
S10P: C30.2, C31.1, C68.1, D12.1 (A), IC1.25 (S10P), R60.2
S11N: C58.2, D11.2 (A), IC1.20 (S11N), R57.2
S11P: C29.2, C30.1, C58.1, D11.1 (A), IC1.21 (S11P), R56.2
S12N: C57.2, D10.2 (A), IC1.17 (S12N), R54.2
S12P: C28.2, C29.1, C57.1, D10.1 (A), IC1.18 (S12P), R53.2
S13N: C53.2, D9.2 (A), IC1.13 (S13N), R50.2
S13P: C27.2, C28.1, C53.1, D9.1 (A), IC1.14 (S13P), R49.2
S14N: C52.2, D8.2 (A), IC1.10 (S14N), R47.2
S14P: C26.2, C27.1, C52.1, D8.1 (A), IC1.11 (S14P), R46.2
S15N: C45.2, D7.2 (A), IC1.6 (S15N), R43.2
S15P: C25.2, C26.1, C45.1, D7.1 (A), IC1.7 (S15P), R41.2
S16N: C42.2, D6.2 (A), IC1.3 (S16N), R42.2
S16P: C25.1, C42.1, D6.1 (A), IC1.4 (S16P), R39.2
V+: C1.1, IC1.1 (V+), R1.2
VREF1: C100.1, IC1.70 (VREF1)
VREF2: C97.1, IC1.68 (VREF2), R17.1, R19.1, R21.1, R25.1, R26.1, R27.1, R31.1, R32.1, R33.1, R35.1
VREG: C4.1, IC1.60 (ISOMD), IC1.69 (VREG), L1.1, TP11.1
Vin: J13.1, JP1.2 (B), R1.1, R2.1, TP9.1
isoSPIA1: C7.2, J14.2, TP6.1
isoSPIA2: C8.2, J14.1, TP5.1
isoSPIB1: C13.2, J15.2, TP2.1
isoSPIB2: C14.2, J15.1, TP1.1

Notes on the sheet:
POWER
isoSPI A
ADBMS6830B
GPIO
isoSPI B

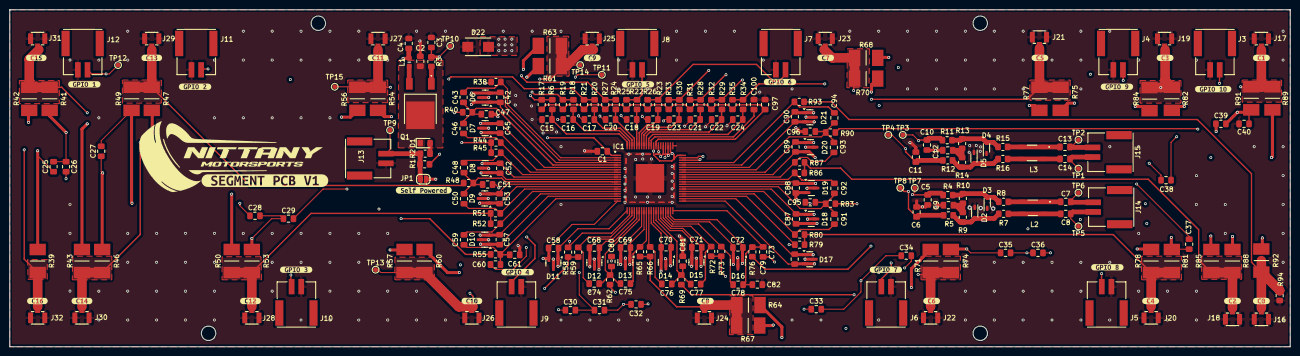
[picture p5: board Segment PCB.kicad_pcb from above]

Board: 4 copper layers, 266.0 x 70.0 mm, 281 parts (1 on the bottom side), 123 nets.

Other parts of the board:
kibuzzard-671AD0BD: G***; kibuzzard-671AD0BD
kibuzzard-671AD1D4: G***; kibuzzard-671AD1D4
kibuzzard-671AD1D9: G***; kibuzzard-671AD1D9
kibuzzard-671AD1E8: G***; kibuzzard-671AD1E8
kibuzzard-671AD1F8: G***; kibuzzard-671AD1F8
kibuzzard-671AD4A2: G***; kibuzzard-671AD4A2
kibuzzard-671AD4AD: G***; kibuzzard-671AD4AD
kibuzzard-671AD4C0: G***; kibuzzard-671AD4C0
kibuzzard-671AD4CD: G***; kibuzzard-671AD4CD
kibuzzard-671AD11F: G***; kibuzzard-671AD11F
kibuzzard-671AD12D: G***; kibuzzard-671AD12D
kibuzzard-671AD13E: G***; kibuzzard-671AD13E
kibuzzard-671AD21F: G***; kibuzzard-671AD21F
kibuzzard-671AD22C: G***; kibuzzard-671AD22C
kibuzzard-671AD51B: G***; kibuzzard-671AD51B
kibuzzard-671AD110: G***; kibuzzard-671AD110
kibuzzard-671AD135: G***; kibuzzard-671AD135
kibuzzard-671AD147: G***; kibuzzard-671AD147
kibuzzard-671AD153: G***; kibuzzard-671AD153
kibuzzard-671AD205: G***; kibuzzard-671AD205
kibuzzard-671AD211: G***; kibuzzard-671AD211
kibuzzard-671AD218: G***; kibuzzard-671AD218
kibuzzard-671AD462: G***; kibuzzard-671AD462
kibuzzard-671AD496: G***; kibuzzard-671AD496
kibuzzard-671AD506: G***; kibuzzard-671AD506
kibuzzard-671AD523: G***; kibuzzard-671AD523
kibuzzard-671AD529: G***; kibuzzard-671AD529
kibuzzard-671ADAE7: G***; kibuzzard-671ADAE7
kibuzzard-671ADDD3: G***; kibuzzard-671ADDD3
kibuzzard-671ADE02: G***; kibuzzard-671ADE02

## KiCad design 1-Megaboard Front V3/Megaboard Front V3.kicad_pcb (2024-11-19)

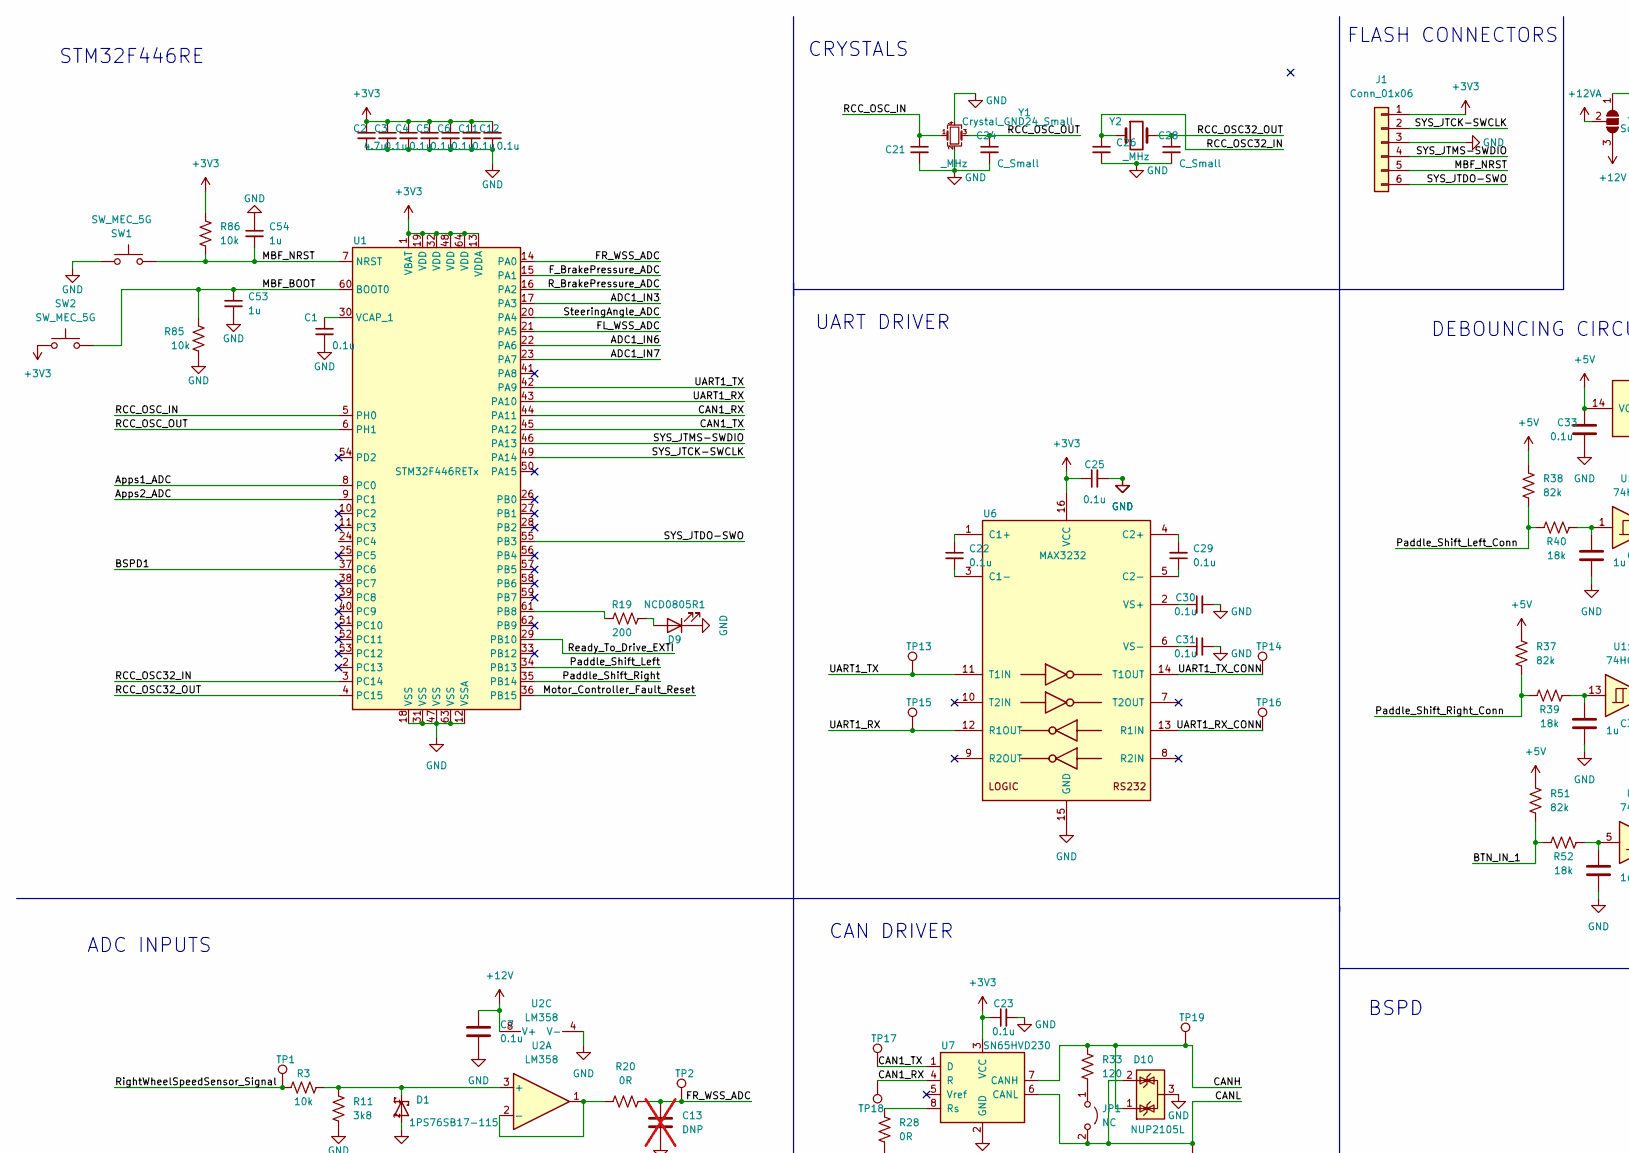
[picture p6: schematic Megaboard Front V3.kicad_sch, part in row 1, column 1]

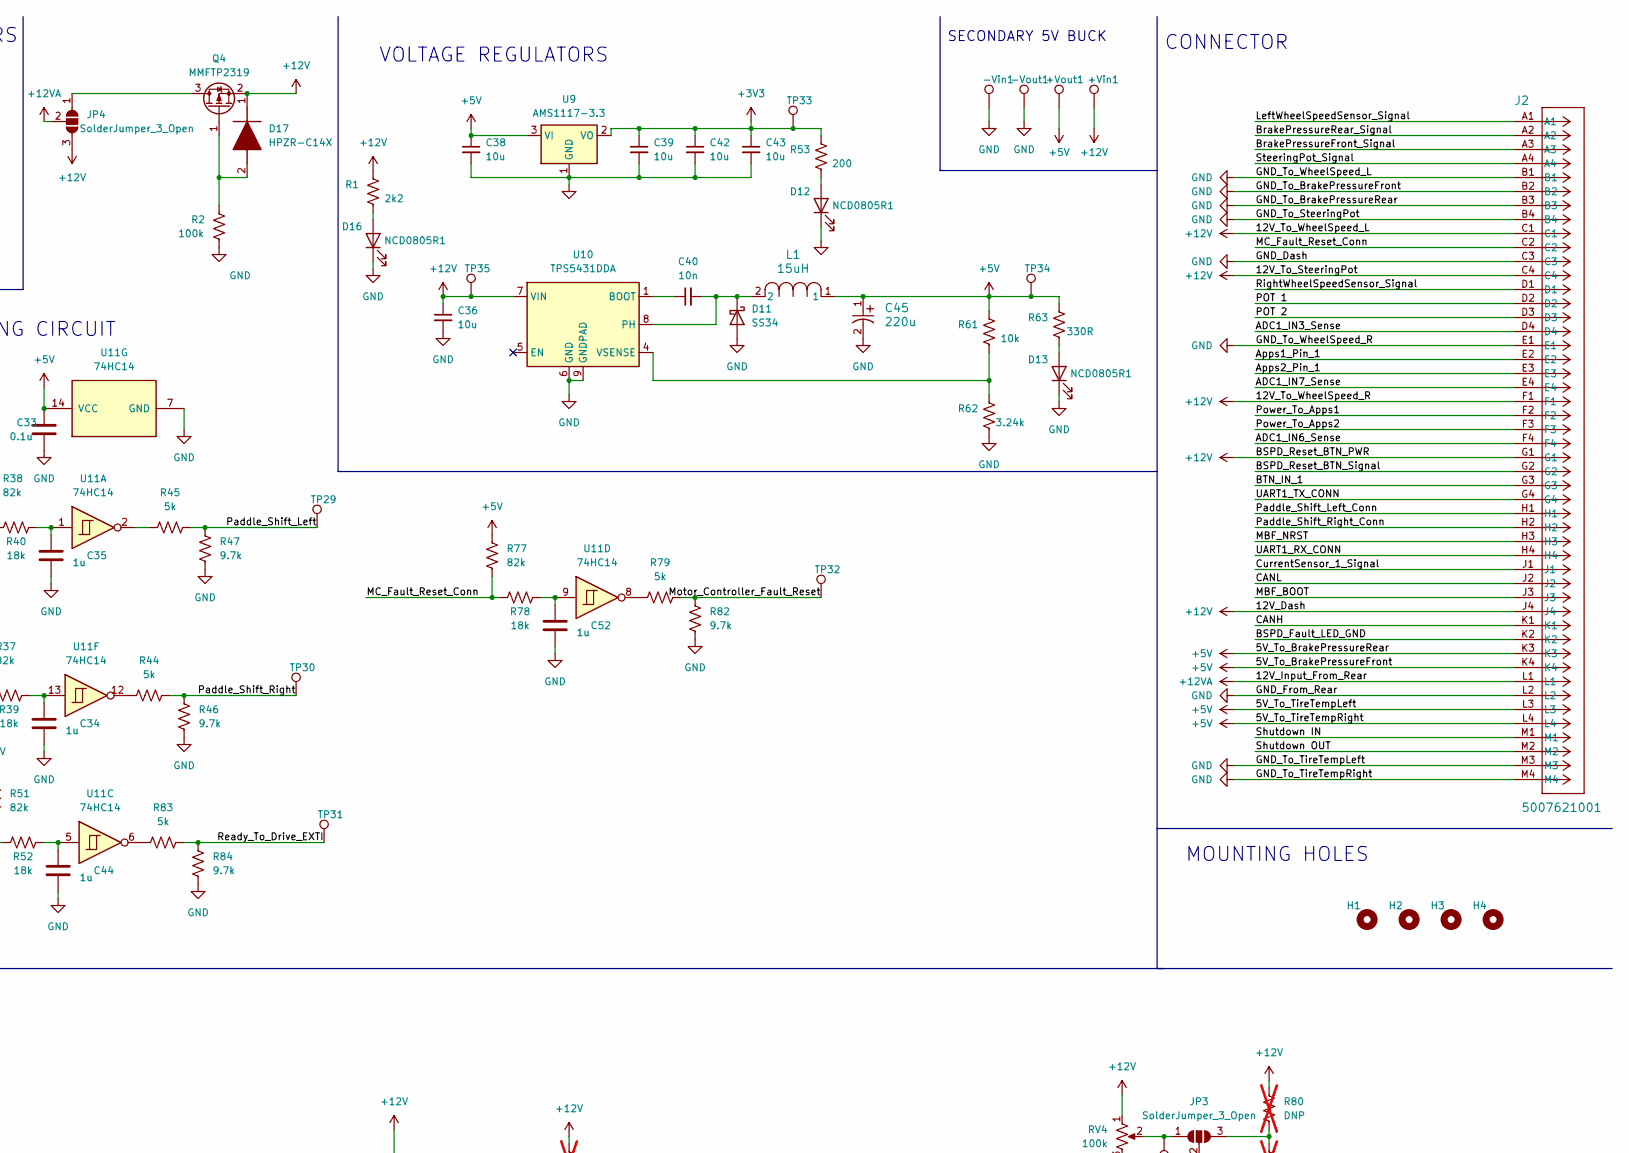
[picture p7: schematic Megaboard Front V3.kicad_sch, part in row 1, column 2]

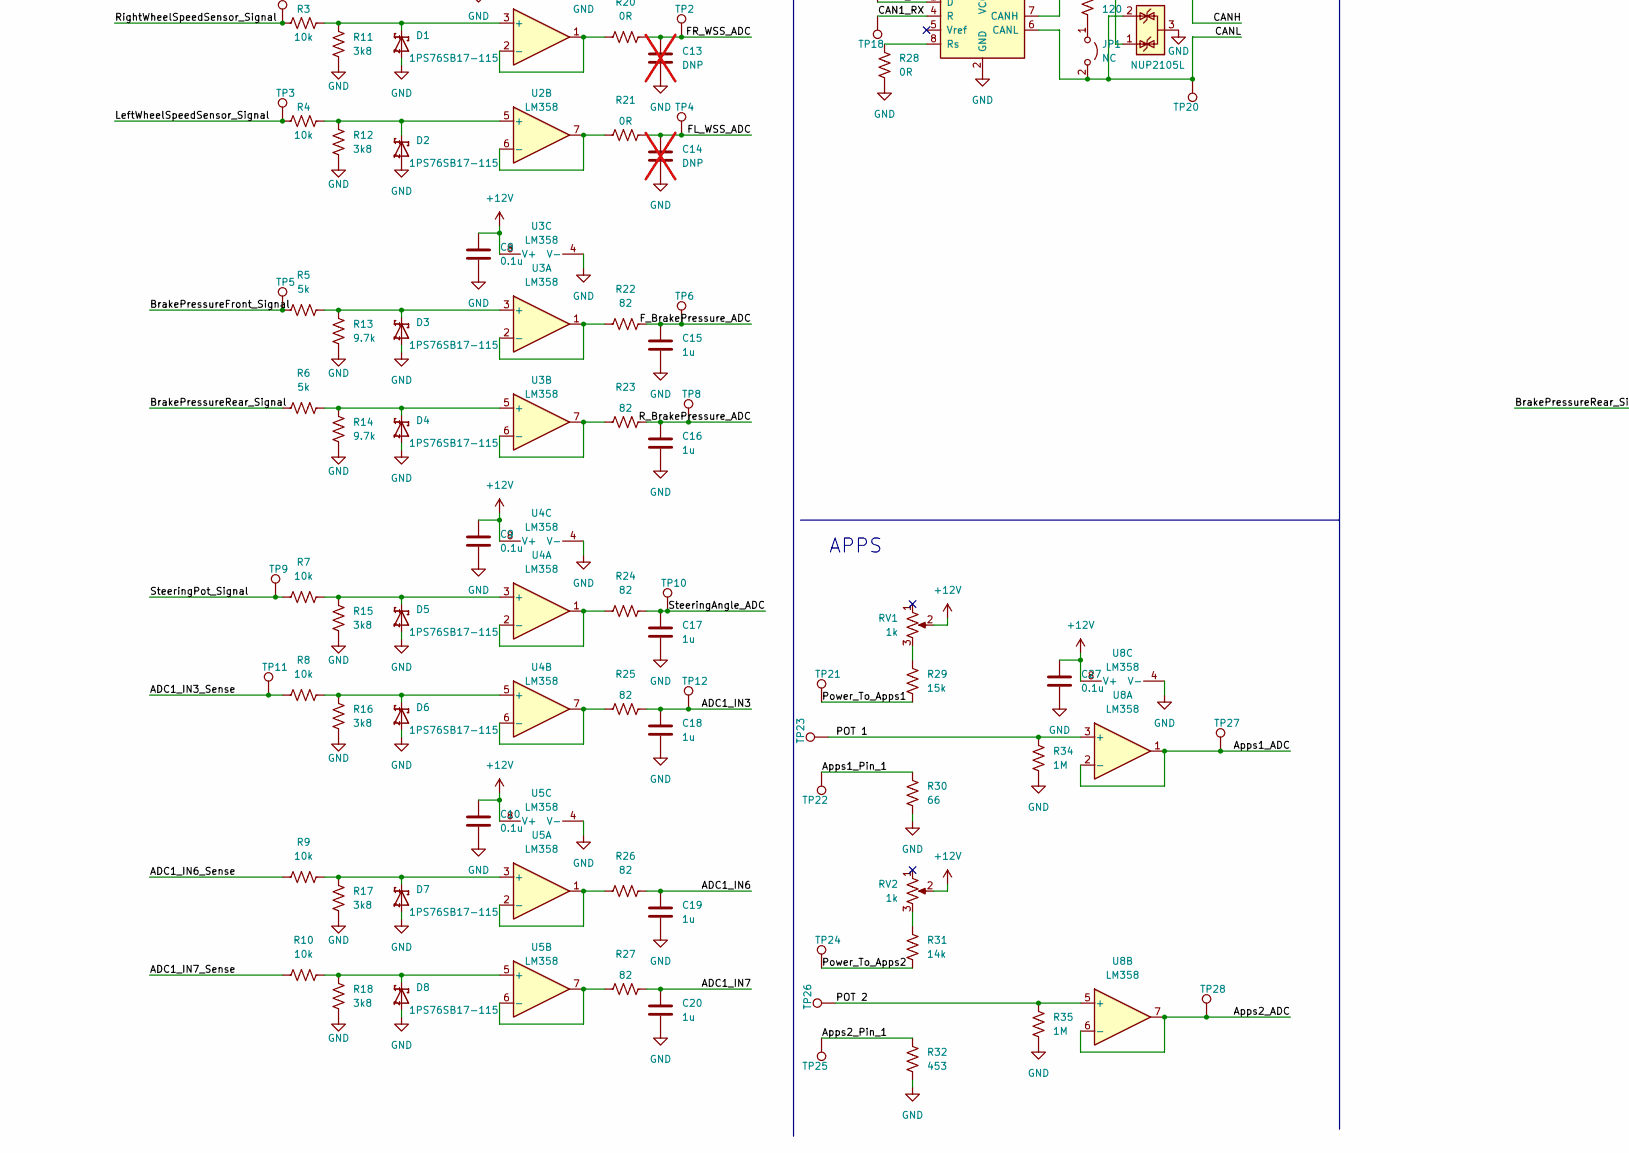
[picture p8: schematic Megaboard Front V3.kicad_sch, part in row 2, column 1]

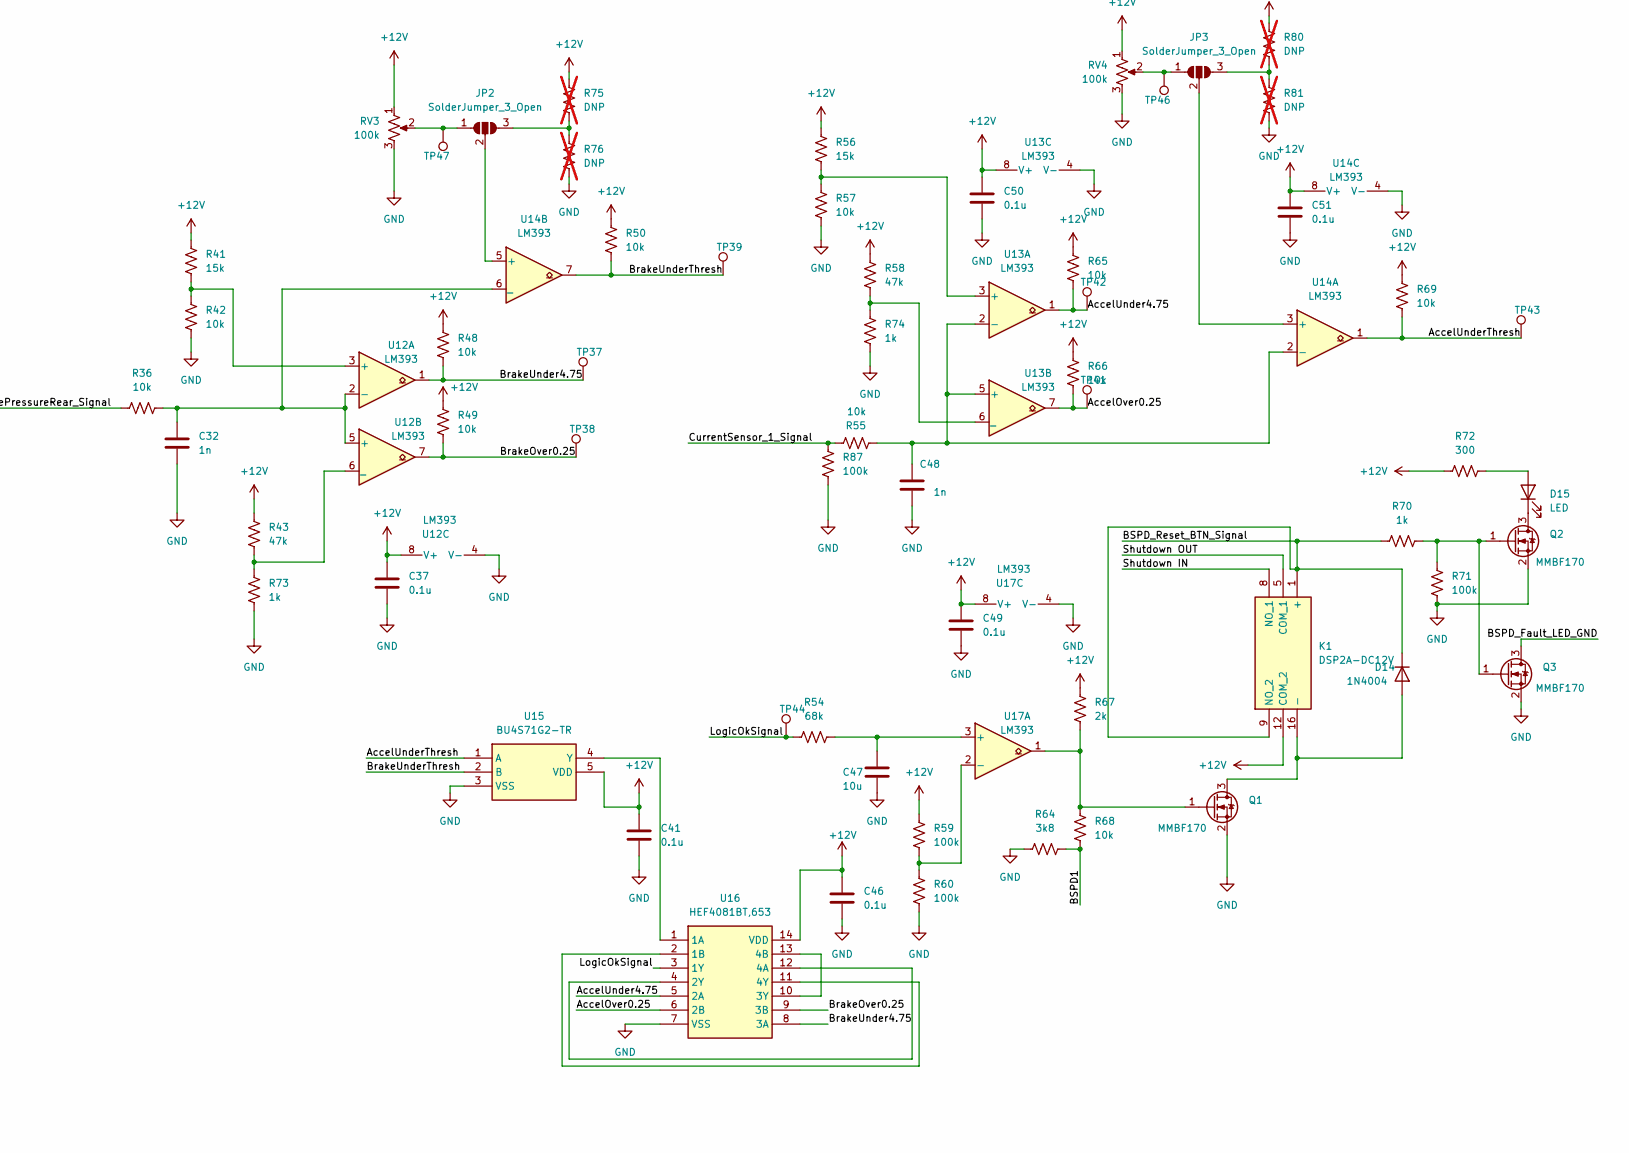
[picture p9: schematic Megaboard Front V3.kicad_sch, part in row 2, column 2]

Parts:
+Vin1: TestPoint_Pad_D1.0mm; MPN DNP; JLCPCB Part # DNP
+Vout1: TestPoint_Pad_D1.0mm; MPN DNP; JLCPCB Part # DNP
-Vin1: TestPoint_Pad_D1.0mm; MPN DNP; JLCPCB Part # DNP
-Vout1: TestPoint_Pad_D1.0mm; MPN DNP; JLCPCB Part # DNP
C1, C3, C4, C5, C6, C11, C12, C22, C23, C25, C29, C30, C31: 0.1u; C_0805_2012Metric_Pad1.18x1.45mm_HandSolder; JLCPCB Part # C49678
C2: 4.7u; C_0805_2012Metric_Pad1.18x1.45mm_HandSolder; JLCPCB Part # C1779
C7, C8, C9, C10, C27, C33: 0.1u; C_0805_2012Metric_Pad1.18x1.45mm_HandSolder; MPN C28233; JLCPCB Part # C49678
C13, C14: DNP; C_0805_2012Metric_Pad1.18x1.45mm_HandSolder; MPN C28323; JLCPCB Part # DNP; not fitted
C15, C16, C17, C18, C19, C20, C34, C35, C44, C52: 1u; C_0805_2012Metric_Pad1.18x1.45mm_HandSolder; MPN C28323; JLCPCB Part # C28323
C21, C26: _MHz; C_0805_2012Metric_Pad1.18x1.45mm_HandSolder; JLCPCB Part # DNP
C24, C28: C_Small; C_0805_2012Metric_Pad1.18x1.45mm_HandSolder; JLCPCB Part # DNP
C32, C48: 1n; C_0805_2012Metric_Pad1.18x1.45mm_HandSolder; MPN C35216; JLCPCB Part # C46653
C36: 10u; C_0805_2012Metric_Pad1.18x1.45mm_HandSolder; MPN C15850; JLCPCB Part # C15850
C37, C41, C46, C49, C50, C51: 0.1u; C_0805_2012Metric_Pad1.18x1.45mm_HandSolder; MPN C35216; JLCPCB Part # C49678
C38, C39, C42, C43: 10u; CP_EIA-3216-18_Kemet-A; MPN C15850; JLCPCB Part # C7171
C40: 10n; C_0805_2012Metric_Pad1.18x1.45mm_HandSolder; MPN C15850; JLCPCB Part # C1710
C45: 220u; PCAP_TPB_D4_PAN; MPN 10TPB220M; JLCPCB Part # C242173
C47: 10u; C_0805_2012Metric_Pad1.18x1.45mm_HandSolder; MPN C13585; JLCPCB Part # C15850
C53, C54: 1u; C_0805_2012Metric_Pad1.18x1.45mm_HandSolder; MPN C15850; JLCPCB Part # C28323
D1, D2, D3, D4, D5, D6, D7, D8: 1PS76SB17-115; SOD323_F_; JLCPCB Part # C551398
D9, D12, D13, D16: NCD0805R1; LED_0805_2012Metric_Pad1.15x1.40mm_HandSolder; MPN C84256; JLCPCB Part # C84256
D10: NUP2105L; SOT-23; JLCPCB Part # C2890118
D11: SS34; D_SMA; JLCPCB Part # C8678
D14: 1N4004; D_SMA_Handsoldering; MPN C95872; JLCPCB Part # C727080
D15: LED; LED_0805_2012Metric_Pad1.15x1.40mm_HandSolder; MPN C2297; JLCPCB Part # C2297
D17: HPZR-C14X; HPZRC14X; Mouser Part Number 771-HPZR-C14X
H1, H2, H3, H4: MountingHole; MountingHole_3.2mm_M3; JLCPCB Part # DNP
J1: Conn_01x06; PinHeader_2x03_P2.54mm_Vertical; JLCPCB Part # DNP
J2: 5007621001; CONN_500762-1001_MOL; JLCPCB Part # DNP
JP1: NC; SolderJumper-2_P1.3mm_Open_RoundedPad1.0x1.5mm; JLCPCB Part # DNP
JP2, JP3, JP4: SolderJumper_3_Open; SolderJumper-3_P1.3mm_Open_RoundedPad1.0x1.5mm
K1: DSP2A-DC12V; RELAY_DSP2A_PAN; Mouser Part Number 769-DSP2A-DC12V
L1: 15uH; IND_CDRH104_SUM; MPN CDRH104RNP-150NC; JLCPCB Part # C225048
Q1, Q2, Q3: MMBF170; SOT-23; MPN C130879; JLCPCB Part # C151058
Q4: MMFTP2319; SOT-23; JLCPCB Part # DNP
R1: 2k2; R_0805_2012Metric_Pad1.20x1.40mm_HandSolder; MPN C17630; JLCPCB Part # C17520
R2: 100k; R_0805_2012Metric_Pad1.20x1.40mm_HandSolder; MPN C17630; JLCPCB Part # C149504
R3, R4, R7, R8, R9, R10: 10k; R_0805_2012Metric_Pad1.20x1.40mm_HandSolder; MPN C23255; JLCPCB Part # C17414
R5, R6, R44, R45, R79, R83: 5k; R_0805_2012Metric_Pad1.20x1.40mm_HandSolder; MPN C23255; JLCPCB Part # C2828700
R11, R12, R15, R16, R17, R18, R64: 3k8; R_0805_2012Metric_Pad1.20x1.40mm_HandSolder; MPN C23255; JLCPCB Part # C228799
R13, R14, R46, R47, R82, R84: 9.7k; R_0805_2012Metric_Pad1.20x1.40mm_HandSolder; MPN C23255; JLCPCB Part # C374689
R19: 200; R_0805_2012Metric_Pad1.20x1.40mm_HandSolder; MPN C706418; JLCPCB Part # C17540
R20, R21: 0R; R_0805_2012Metric_Pad1.20x1.40mm_HandSolder; MPN C23255; JLCPCB Part # C17477
R22, R23, R24, R25, R26, R27: 82; R_0805_2012Metric_Pad1.20x1.40mm_HandSolder; MPN C23255; JLCPCB Part # C17841
R28: 0R; R_0805_2012Metric_Pad1.20x1.40mm_HandSolder; MPN C21189; JLCPCB Part # C17477
R29: 15k; R_0805_2012Metric_Pad1.20x1.40mm_HandSolder; JLCPCB Part # C17475
R30: 66; R_0805_2012Metric_Pad1.20x1.40mm_HandSolder
R31: 14k; R_0805_2012Metric_Pad1.20x1.40mm_HandSolder; JLCPCB Part # C17464
R32: 453; R_0805_2012Metric_Pad1.20x1.40mm_HandSolder
R33: 120; R_0805_2012Metric_Pad1.20x1.40mm_HandSolder; MPN C22787; JLCPCB Part # C17437
R34, R35: 1M; R_0805_2012Metric_Pad1.20x1.40mm_HandSolder; JLCPCB Part # C17514
R36, R48, R49, R50, R55, R65, R66, R69: 10k; R_0805_2012Metric_Pad1.20x1.40mm_HandSolder; MPN C17902; JLCPCB Part # C17414
R37, R38, R51, R77: 82k; R_0805_2012Metric_Pad1.20x1.40mm_HandSolder; MPN C23186; JLCPCB Part # C17840
R39, R40, R52, R78: 18k; R_0805_2012Metric_Pad1.20x1.40mm_HandSolder; MPN C22809; JLCPCB Part # C17506
R41, R56: 15k; R_0805_2012Metric_Pad1.20x1.40mm_HandSolder; MPN C706418; JLCPCB Part # C17475
R42, R57: 10k; R_0805_2012Metric_Pad1.20x1.40mm_HandSolder; MPN C706423; JLCPCB Part # C17414
R43, R58: 47k; R_0805_2012Metric_Pad1.20x1.40mm_HandSolder; MPN C706418; JLCPCB Part # C17713
R53: 200; R_0805_2012Metric_Pad1.20x1.40mm_HandSolder; MPN C17520; JLCPCB Part # C17540
R54: 68k; R_0805_2012Metric_Pad1.20x1.40mm_HandSolder; MPN C73040; JLCPCB Part # C17801
R59, R60, R71, R87: 100k; R_0805_2012Metric_Pad1.20x1.40mm_HandSolder; MPN C17900; JLCPCB Part # C149504
R61: 10k; R_0805_2012Metric_Pad1.20x1.40mm_HandSolder; MPN C17540; JLCPCB Part # C17414
R62: 3.24k; R_0805_2012Metric_Pad1.20x1.40mm_HandSolder; MPN C17540; JLCPCB Part # C4194377
R63: 330R; R_0805_2012Metric_Pad1.20x1.40mm_HandSolder; MPN C17630; JLCPCB Part # C17630
R67: 2k; R_0805_2012Metric_Pad1.20x1.40mm_HandSolder; MPN C4410; JLCPCB Part # C17604
R68: 10k; R_0805_2012Metric_Pad1.20x1.40mm_HandSolder; MPN C4410; JLCPCB Part # C17414
R70: 1k; R_0805_2012Metric_Pad1.20x1.40mm_HandSolder; MPN C4410; JLCPCB Part # C17513
R72: 300; R_0805_2012Metric_Pad1.20x1.40mm_HandSolder; MPN C17909; JLCPCB Part # C17617
R73, R74: 1k; R_0805_2012Metric_Pad1.20x1.40mm_HandSolder; MPN C706423; JLCPCB Part # C17513
R75, R76, R80, R81: DNP; R_0805_2012Metric_Pad1.20x1.40mm_HandSolder; MPN C706418; JLCPCB Part # C865361; not fitted
R85, R86: 10k; R_0805_2012Metric_Pad1.20x1.40mm_HandSolder; MPN C17414; JLCPCB Part # C17414
RV1, RV2: 1k; Potentiometer_Bourns_3296W_Vertical; MPN C83686
RV3, RV4: 100k; Potentiometer_Bourns_3296W_Vertical; MPN C83686
SW1: SW_MEC_5G; SW_Push_1P1T_XKB_TS-1187A; MPN C318884; JLCPCB Part # C318884
SW2: SW_MEC_5G; SW_Push_1P1T_XKB_TS-1187A; JLCPCB Part # C318884
TP1, TP2, TP3, TP4, TP5, TP6, TP8, TP9, TP10, TP11, TP12, TP13, TP14, TP15, TP16, TP17, TP18, TP19, TP20, TP21, TP22, TP23, TP24, TP25, TP26, TP27, TP28, TP29, TP30, TP31, TP32, TP33, TP34, TP35, TP37, TP38, TP39, TP41, TP42, TP43, TP44, TP46, TP47: TestPoint_Pad_D1.0mm; MPN DNP; JLCPCB Part # DNP
U1: STM32F446RETx; LQFP-64_10x10mm_P0.5mm; JLCPCB Part # C69336
U2, U3, U4, U5, U8: LM358; SOIC-8_3.9x4.9mm_P1.27mm; MPN C7950; JLCPCB Part # C9418
U6: MAX3232; SOIC-16_3.9x9.9mm_P1.27mm; JLCPCB Part # C18261
U7: SN65HVD230; SOIC-8_3.9x4.9mm_P1.27mm; MPN C12084; JLCPCB Part # C12084
U9: AMS1117-3.3; SOT-223-3_TabPin2; JLCPCB Part # C6186
U10: TPS5431DDA; TI_SO-PowerPAD-8_ThermalVias; JLCPCB Part # C9864
U11: 74HC14; SOIC-14_3.9x8.7mm_P1.27mm; MPN C5605; JLCPCB Part # C5605
U12, U13, U14, U17: LM393; SOIC-8_3.9x4.9mm_P1.27mm; MPN C7955; JLCPCB Part # C32901
U15: BU4S71G2-TR; SOT95P280X125-5N; Mouser Part Number 755-BU4S71G2-TR
U16: HEF4081BT,653; SOIC127P600X175-14N; Mouser Part Number 771-HEF4081BTD-T
Y1: Crystal_GND24_Small; Crystal_SMD_3225-4Pin_3.2x2.5mm_HandSoldering
Y2: Crystal_GND23_Small; Crystal_SMD_3215-2Pin_3.2x1.5mm; JLCPCB Part # DNP

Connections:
+3V3: C2.1, C3.1, C4.1, C5.1, C6.1, C11.1, C12.1, C23.1, C25.1, C39.1, C42.1, C43.1, J1.1, R53.1, R86.1, SW2.1 (A), TP33.1, U1.1 (VBAT), U1.13 (VDDA), U1.19 (VDD), U1.32 (VDD), U1.48 (VDD), U1.64 (VDD), U6.16 (VCC), U7.3 (VCC), U9.2 (VO)
+5V: +Vout1.1, C33.1, C38.1, C45.1, J2.K3, J2.K4, J2.L3, J2.L4, L1.1, R37.1, R38.1, R51.1, R61.1, R63.1, R77.1, TP34.1, U9.3 (VI), U11.14 (VCC)
+12V: +Vin1.1, C7.1, C8.1, C9.1, C10.1, C27.1, C36.1, C37.1, C41.1, C46.1, C49.1, C50.1, C51.1, D17.1 (K), J2.C1, J2.C4, J2.F1, J2.G1, J2.J4, JP4.3 (B), K1.12 (COM_2), Q4.2 (S), R1.1, R41.1, R43.1, R48.1, R49.1, R50.1, R56.1, R58.1, R59.1, R65.1, R66.1, R67.1, R69.1, R72.1, R75.1, R80.1, RV1.2, RV2.2, RV3.1, RV4.1, TP35.1, U2.8 (V+), U3.8 (V+), U4.8 (V+), U5.8 (V+), U8.8 (V+), U10.7 (VIN), U12.8 (V+), U13.8 (V+), U14.8 (V+), U15.5 (VDD), U16.14 (VDD), U17.8 (V+)
+12VA: J2.L1, JP4.2 (C)
/ADC1_IN3: C18.1, R25.2, TP12.1, U1.17 (PA3)
/ADC1_IN3_Sense: J2.D4, R8.1, TP11.1
/ADC1_IN6: C19.1, R26.2, U1.22 (PA6)
/ADC1_IN6_Sense: J2.F4, R9.1
/ADC1_IN7: C20.1, R27.2, U1.23 (PA7)
/ADC1_IN7_Sense: J2.E4, R10.1
/AccelOver0.25: R66.2, TP41.1, U13.7, U16.6 (2B)
/AccelUnder4.75: R65.2, TP42.1, U13.1, U16.5 (2A)
/AccelUnderThresh: R69.2, TP43.1, U14.1, U15.1 (A)
/Apps1_ADC: TP27.1, U1.8 (PC0), U8.1, U8.2 (-)
/Apps1_Pin_1: J2.E2, R30.2, TP22.1
/Apps2_ADC: TP28.1, U1.9 (PC1), U8.6 (-), U8.7
/Apps2_Pin_1: J2.E3, R32.2, TP25.1
/BSPD1: R64.2, R68.2, U1.37 (PC6)
/BSPD_Fault_LED_GND: J2.K2, Q3.3 (D)
/BSPD_Reset_BTN_Signal: D14.1 (K), J2.G2, K1.1 (+), K1.9 (NO_2), R70.1
/BTN_IN_1: J2.G3, R51.2, R52.1
/BrakeOver0.25: R49.2, TP38.1, U12.7, U16.9 (3B)
/BrakePressureFront_Signal: J2.A3, R5.1, TP5.1
/BrakePressureRear_Signal: J2.A2, R6.1, R36.1
/BrakeUnder4.75: R48.2, TP37.1, U12.1, U16.8 (3A)
/BrakeUnderThresh: R50.2, TP39.1, U14.7, U15.2 (B)
/CAN1_RX: TP18.1, U1.44 (PA11), U7.4 (R)
/CAN1_TX: TP17.1, U1.45 (PA12), U7.1 (D)
/CANH: D10.1 (K), J2.K1, R33.2, TP19.1, U7.7 (CANH)
/CANL: D10.2 (K), J2.J2, JP1.2 (B), TP20.1, U7.6 (CANL)
/CurrentSensor_1_Signal: J2.J1, R55.1, R87.1
/FL_WSS_ADC: C14.1, R21.2, TP4.1, U1.21 (PA5)
/FR_WSS_ADC: C13.1, R20.2, TP2.1, U1.14 (PA0)
/F_BrakePressure_ADC: C15.1, R22.2, TP6.1, U1.15 (PA1)
/LeftWheelSpeedSensor_Signal: J2.A1, R4.1, TP3.1
/LogicOkSignal: R54.1, TP44.1, U16.3 (1Y)
/MBF_BOOT: C53.1, J2.J3, R85.1, SW2.2 (B), U1.60 (BOOT0)
/MBF_NRST: C54.2, J1.5, J2.H3, R86.2, SW1.2 (B), U1.7 (NRST)
/MC_Fault_Reset_Conn: J2.C2, R77.2, R78.1
/Motor_Controller_Fault_Reset: R79.2, R82.2, TP32.1, U1.36 (PB15)
/POT 1: J2.D2, R34.1, TP23.1, U8.3 (+)
/POT 2: J2.D3, R35.1, TP26.1, U8.5 (+)
/Paddle_Shift_Left: R45.2, R47.2, TP29.1, U1.34 (PB13)
/Paddle_Shift_Left_Conn: J2.H1, R38.2, R40.1
/Paddle_Shift_Right: R44.2, R46.2, TP30.1, U1.35 (PB14)
/Paddle_Shift_Right_Conn: J2.H2, R37.2, R39.1
/Power_To_Apps1: J2.F2, R29.2, TP21.1
/Power_To_Apps2: J2.F3, R31.2, TP24.1
/RCC_OSC32_IN: C26.1, U1.3 (PC14), Y2.1
/RCC_OSC32_OUT: C28.1, U1.4 (PC15), Y2.2
/RCC_OSC_IN: C21.1, U1.5 (PH0), Y1.1
/RCC_OSC_OUT: C24.1, U1.6 (PH1), Y1.3
/R_BrakePressure_ADC: C16.1, R23.2, TP8.1, U1.16 (PA2)
/Ready_To_Drive_EXTI: R83.2, R84.2, TP31.1, U1.29 (PB10)
/RightWheelSpeedSensor_Signal: J2.D1, R3.1, TP1.1
/SYS_JTCK-SWCLK: J1.2, U1.49 (PA14)
/SYS_JTDO-SWO: J1.6, U1.55 (PB3)
/SYS_JTMS-SWDIO: J1.4, U1.46 (PA13)
/Shutdown IN: J2.M1, K1.8 (NO_1)
/Shutdown OUT: J2.M2, K1.5 (COM_1)
/SteeringAngle_ADC: C17.1, R24.2, TP10.1, U1.20 (PA4)
/SteeringPot_Signal: J2.A4, R7.1, TP9.1
/UART1_RX: TP15.1, U1.43 (PA10), U6.12 (R1OUT)
/UART1_RX_CONN: J2.H4, TP16.1, U6.13 (R1IN)
/UART1_TX: TP13.1, U1.42 (PA9), U6.11 (T1IN)
/UART1_TX_CONN: J2.G4, TP14.1, U6.14 (T1OUT)
GND: -Vin1.1, -Vout1.1, C1.2, C2.2, C3.2, C4.2, C5.2, C6.2, C7.2, C8.2, C9.2, C10.2, C11.2, C12.2, C13.2, C14.2, C15.2, C16.2, C17.2, C18.2, C19.2, C20.2, C21.2, C23.2, C24.2, C25.2, C26.2, C27.2, C28.2, C30.2, C31.2, C32.2, C33.2, C34.2, C35.2, C36.2, C37.2, C38.2, C39.2, C41.2, C42.2, C43.2, C44.2, C45.2, C46.2, C47.2, C48.2, C49.2, C50.2, C51.2, C52.2, C53.2, C54.1, D1.2, D2.2, D3.2, D4.2, D5.2, D6.2, D7.2, D8.2, D9.1 (K), D10.3 (A), D11.2 (A), D12.1 (K), D13.1 (K), D16.1 (K), J1.3, J2.B1, J2.B2, J2.B3, J2.B4, J2.C3, J2.E1, J2.L2, J2.M3, J2.M4, Q1.2 (S), Q2.2 (S), Q3.2 (S), R2.2, R11.1, R12.1, R13.1, R14.1, R15.1, R16.1, R17.1, R18.1, R28.2, R30.1, R32.1, R34.2, R35.2, R42.2, R46.1, R47.1, R57.2, R60.2, R62.2, R64.1, R71.1, R73.2, R74.2, R76.2, R81.2, R82.1, R84.1, R85.2, R87.2, RV3.3, RV4.3, SW1.1 (A), U1.12 (VSSA), U1.18 (VSS), U1.31 (VSS), U1.47 (VSS), U1.63 (VSS), U2.4 (V-), U3.4 (V-), U4.4 (V-), U5.4 (V-), U6.15 (GND), U7.2 (GND), U8.4 (V-), U9.1 (GND), U10.6 (GND), U10.9 (GNDPAD), U11.7 (GND), U12.4 (V-), U13.4 (V-), U14.4 (V-), U15.3 (VSS), U16.7 (VSS), U17.4 (V-), Y1.2, Y1.4
unnamed: C34.1, R39.2, U11.13
unnamed: C35.1, R40.2, U11.1
unnamed: C44.1, R52.2, U11.5
unnamed: C52.1, R78.2, U11.9
unnamed: D9.2 (A), R19.1
unnamed: C40.2, D11.1 (K), L1.2, U10.8 (PH)
unnamed: D12.2 (A), R53.2
unnamed: D13.2 (A), R63.2
unnamed: D14.2 (A), K1.16 (-), Q1.3 (D)
unnamed: D15.2 (A), R72.2
unnamed: D15.1 (K), Q2.3 (D)
unnamed: D16.2 (A), R1.2
unnamed: D17.2 (A), Q4.1 (G), R2.1
unnamed: JP1.1 (A), R33.1
unnamed: JP2.1 (A), RV3.2, TP47.1
unnamed: JP2.3 (B), R75.2, R76.1
unnamed: JP2.2 (C), U14.5 (+)
unnamed: JP3.1 (A), RV4.2, TP46.1
unnamed: JP3.3 (B), R80.2, R81.1
unnamed: JP3.2 (C), U14.3 (+)
unnamed: JP4.1 (A), Q4.3 (D)
unnamed: Q1.1 (G), R67.2, R68.1, U17.1
unnamed: Q2.1 (G), Q3.1 (G), R70.2, R71.2
unnamed: R29.1, RV1.3
unnamed: R31.1, RV2.3
unnamed: R44.1, U11.12
unnamed: R45.1, U11.2
unnamed: R79.1, U11.8
unnamed: R83.1, U11.6
unnamed: R19.2, U1.61 (PB8)
unnamed: C1.1, U1.30 (VCAP_1)
unnamed: D1.1, R3.2, R11.2, U2.3 (+)
unnamed: R20.1, U2.1, U2.2 (-)
unnamed: D2.1, R4.2, R12.2, U2.5 (+)
unnamed: R21.1, U2.6 (-), U2.7
unnamed: D3.1, R5.2, R13.2, U3.3 (+)
unnamed: R22.1, U3.1, U3.2 (-)
unnamed: D4.1, R6.2, R14.2, U3.5 (+)
unnamed: R23.1, U3.6 (-), U3.7
unnamed: D5.1, R7.2, R15.2, U4.3 (+)
unnamed: R24.1, U4.1, U4.2 (-)
unnamed: D6.1, R8.2, R16.2, U4.5 (+)
unnamed: R25.1, U4.6 (-), U4.7
unnamed: D7.1, R9.2, R17.2, U5.3 (+)
unnamed: R26.1, U5.1, U5.2 (-)
unnamed: D8.1, R10.2, R18.2, U5.5 (+)
unnamed: R27.1, U5.6 (-), U5.7
unnamed: C22.1, U6.1 (C1+)
unnamed: C22.2, U6.3 (C1-)
unnamed: C29.2, U6.4 (C2+)
unnamed: C29.1, U6.5 (C2-)
unnamed: C30.1, U6.2 (VS+)
unnamed: C31.1, U6.6 (VS-)
unnamed: R28.1, U7.8 (Rs)
unnamed: C40.1, U10.1 (BOOT)
unnamed: R61.2, R62.1, U10.4 (VSENSE)
unnamed: R41.2, R42.1, U12.3 (+)
unnamed: C32.1, R36.2, U12.2 (-), U12.5 (+), U14.6 (_)
unnamed: R43.2, R73.1, U12.6 (_)
unnamed: R56.2, R57.1, U13.3 (+)
unnamed: C48.1, R55.2, U13.2 (-), U13.5 (+), U14.2 (-)
unnamed: R58.2, R74.1, U13.6 (_)
unnamed: U15.4 (Y), U16.1 (1A)
unnamed: U16.2 (1B), U16.11 (4Y)
unnamed: U16.4 (2Y), U16.12 (4A)
unnamed: U16.10 (3Y), U16.13 (4B)
unnamed: C47.1, R54.2, U17.3 (+)
unnamed: R59.2, R60.1, U17.2 (-)

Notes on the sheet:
MOUNTING HOLES
UART DRIVER
CAN DRIVER
VOLTAGE REGULATORS
BSPD
STM32F446RE
FLASH CONNECTORS
CRYSTALS
SECONDARY 5V BUCK
DEBOUNCING CIRCUIT
APPS
ADC INPUTS
CONNECTOR

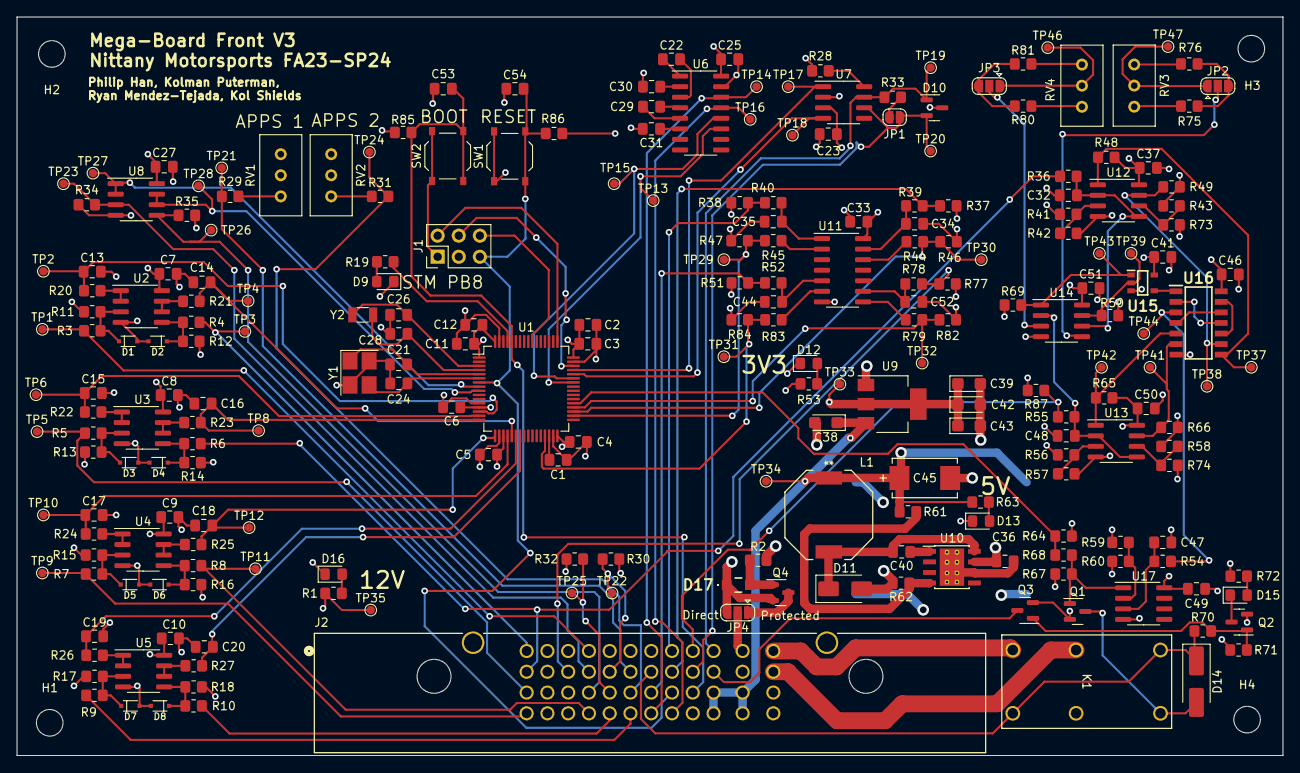
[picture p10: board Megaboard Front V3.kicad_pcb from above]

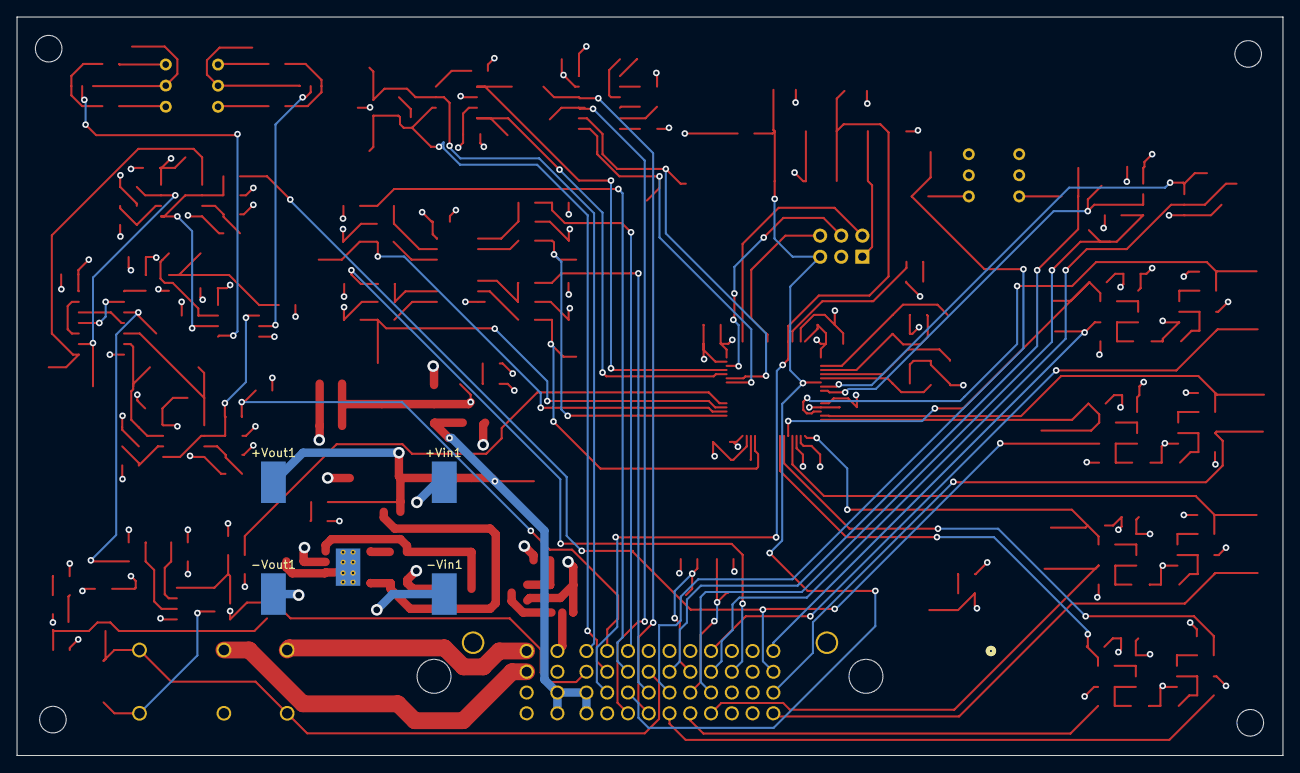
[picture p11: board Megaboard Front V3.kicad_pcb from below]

Board: 4 copper layers, 152.4 x 88.9 mm, 246 parts (4 on the bottom side), 135 nets.

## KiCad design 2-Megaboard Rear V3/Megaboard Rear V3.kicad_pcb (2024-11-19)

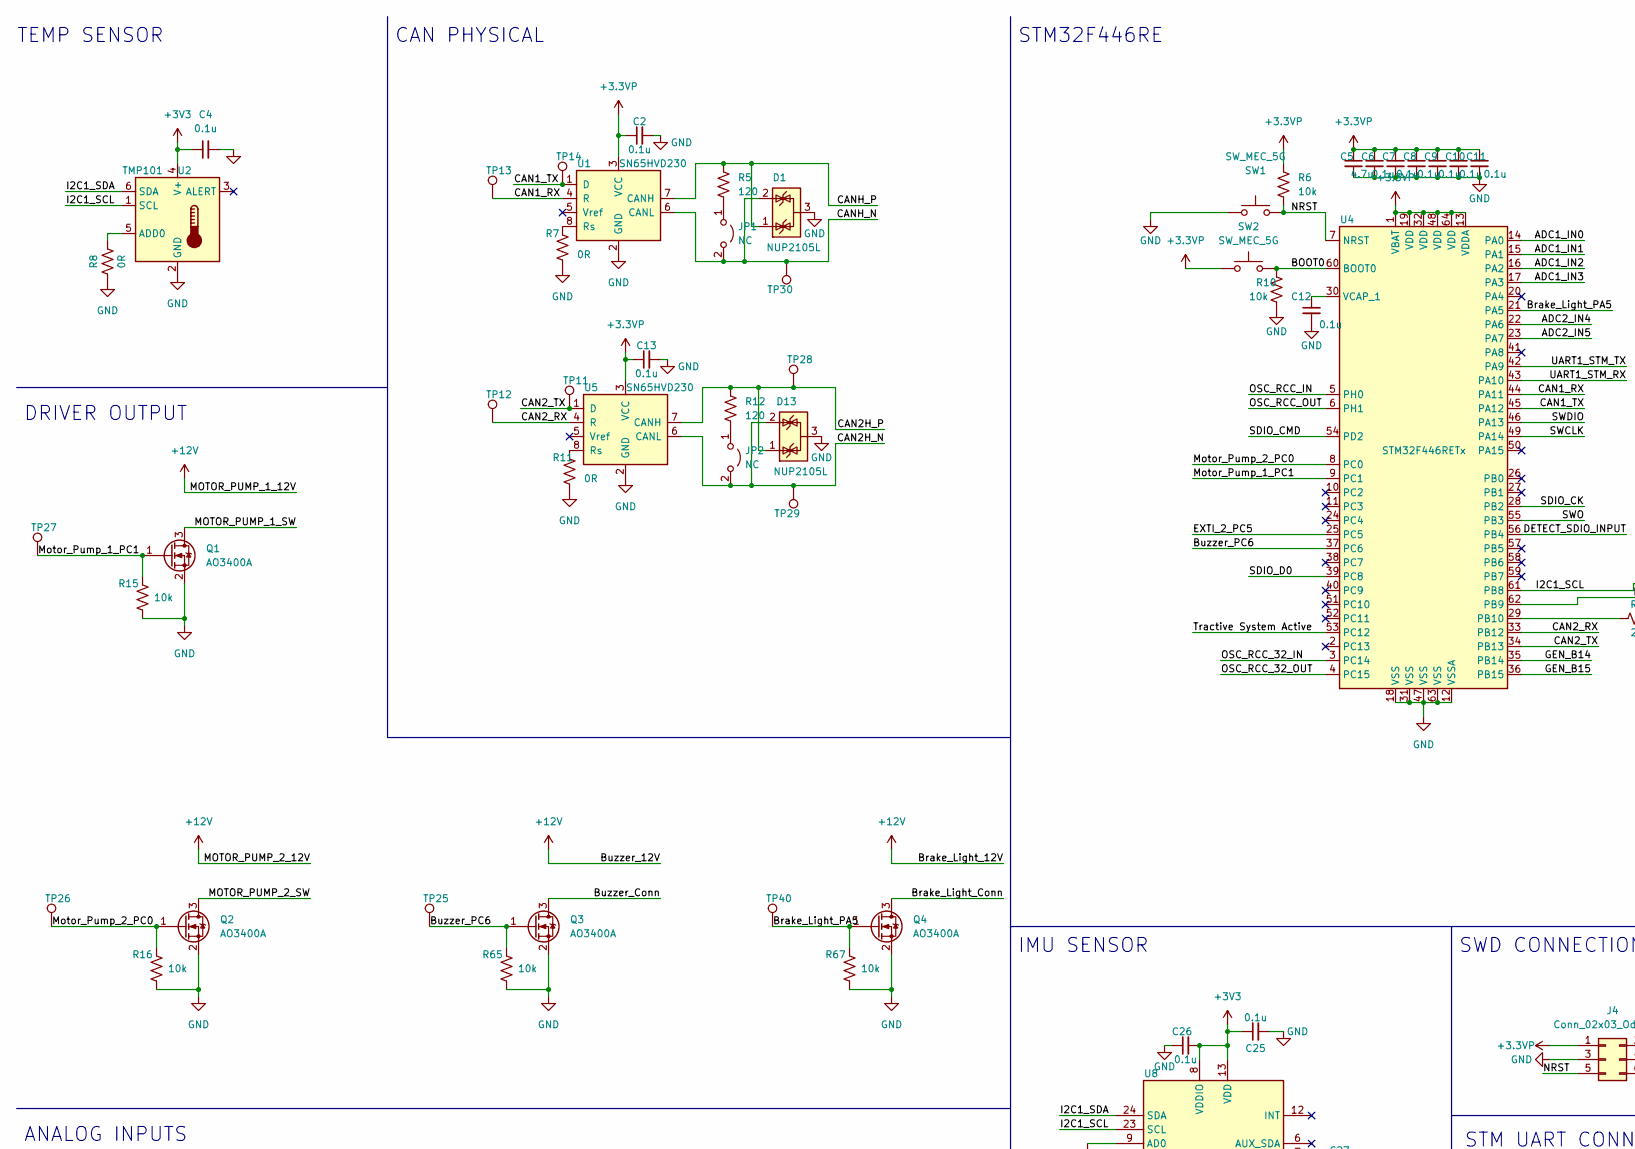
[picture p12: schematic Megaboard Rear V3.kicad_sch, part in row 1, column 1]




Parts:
C1, C2, C3, C4, C6, C7, C8, C9, C10, C11, C12, C13, C14, C15, C16, C17, C20, C25, C26, C28, C30, C31, C38, C43: 0.1u; C_0805_2012Metric_Pad1.18x1.45mm_HandSolder; MPN C28233; JLCPCB Part # C28233
C5: 4.7u; C_0805_2012Metric_Pad1.18x1.45mm_HandSolder; MPN C1779; JLCPCB Part # C1779
C18, C19, C36, C37, C39, C40, C46, C47: 10u; CP_EIA-3216-18_Kemet-A; MPN C15850; JLCPCB Part # C7171
C21, C22: 20p; C_0805_2012Metric_Pad1.18x1.45mm_HandSolder; MPN C1798; JLCPCB Part # C1798
C23, C24: 22p; C_0805_2012Metric_Pad1.18x1.45mm_HandSolder; MPN C1804; JLCPCB Part # C1804
C27, C29: 2.2n; C_0805_2012Metric_Pad1.18x1.45mm_HandSolder; MPN C28260; JLCPCB Part # C28260
C32, C35, C41, C42, C44, C45, C51: 1u; C_0805_2012Metric_Pad1.18x1.45mm_HandSolder; MPN C28323; JLCPCB Part # C28323
C33: 10n; C_0805_2012Metric_Pad1.18x1.45mm_HandSolder; MPN C1710; JLCPCB Part # C1710
C34, C48: 10u; C_0805_2012Metric_Pad1.18x1.45mm_HandSolder; MPN C15850; JLCPCB Part # C15850
C49: 10n; C_0805_2012Metric_Pad1.18x1.45mm_HandSolder; MPN C15850; JLCPCB Part # C1710
C50: 220u; PCAP_TPB_D4_PAN; MPN 10TPB220M; JLCPCB Part # C242173
C52: DNP; C_0805_2012Metric_Pad1.18x1.45mm_HandSolder; MPN C15850; JLCPCB Part # DNP
D1, D13: NUP2105L; SOT-23; MPN DNP; JLCPCB Part # C284104
D2, D4, D14, D15, D16, D17, D19: NCD0805R1; LED_0805_2012Metric_Pad1.15x1.40mm_HandSolder; MPN C84256; JLCPCB Part # C84256
D3: US1M; D_SMA; MPN C412437; JLCPCB Part # C412437
D5: BZV55C15; D_MiniMELF; MPN DNP; JLCPCB Part # C545332
D6, D7, D9, D10, D11, D12: ZMM3V3-M; D_MiniMELF; MPN C8056; JLCPCB Part # DNP
D8: KT-0805G; LED_0805_2012Metric_Pad1.15x1.40mm_HandSolder; MPN C2297; JLCPCB Part # C2297
D18: SS34; D_SMA; JLCPCB Part # C8678
H1, H2, H3, H4: MountingHole; MountingHole_3.2mm_M3; MPN DNP; JLCPCB Part # DNP
HV+1: HIL_TSAL_HV_GND; TestPoint_Pad_D1.0mm; MPN DNP; JLCPCB Part # DNP
HV-1: HIL_TSAL_HV_GND; TestPoint_Pad_D1.0mm; MPN DNP; JLCPCB Part # DNP
J1: 5007621001; CONN_500762-1001_MOL; MPN DNP; JLCPCB Part # DNP
J2: Micro_SD_Card_Det; microSD_HC_Molex_104031-0811; MPN C585350; JLCPCB Part # C585350
J3: Conn_01x03; PinHeader_1x03_P2.54mm_Vertical; JLCPCB Part # DNP
J4: Conn_02x03_Odd_Even; PinHeader_2x03_P2.54mm_Vertical; JLCPCB Part # DNP
J5: Conn_01x04; PinHeader_1x04_P2.54mm_Vertical; MPN DNP; JLCPCB Part # DNP
JP1, JP2: NC; SolderJumper-2_P1.3mm_Open_RoundedPad1.0x1.5mm; MPN DNP; JLCPCB Part # DNP
JP3, JP4, JP7, JP8: SolderJumper_3_Open; SolderJumper-3_P1.3mm_Open_RoundedPad1.0x1.5mm; JLCPCB Part # DNP
JP5, JP6: Jumper_2_Open; SolderJumper-2_P1.3mm_Open_RoundedPad1.0x1.5mm; JLCPCB Part # DNP
L1: 15uH; IND_CDRH104_SUM; MPN CDRH104RNP-150NC; JLCPCB Part # C225048
Q1, Q2, Q3, Q4: AO3400A; SOT-23; MPN C20917; JLCPCB Part # C20917
Q5, Q6, Q7, Q8, Q9: MMBF170; SOT-23; MPN C20917; JLCPCB Part # C130879
R1: 10k; R_0805_2012Metric_Pad1.20x1.40mm_HandSolder; MPN C25804; JLCPCB Part # C17414
R2, R4: 4k7; R_0805_2012Metric_Pad1.20x1.40mm_HandSolder; MPN C23162; JLCPCB Part # C17673
R3, R6, R10, R15, R16, R35, R42, R44, R65, R67: 10k; R_0805_2012Metric_Pad1.20x1.40mm_HandSolder; MPN C17414; JLCPCB Part # C17414
R5, R12: 120; R_0805_2012Metric_Pad1.20x1.40mm_HandSolder; MPN C22787; JLCPCB Part # C17437
R7, R8, R11, R20: 0R; R_0805_2012Metric_Pad1.20x1.40mm_HandSolder; MPN C17477; JLCPCB Part # C17477
R9, R17: 200; R_0805_2012Metric_Pad1.20x1.40mm_HandSolder; MPN C17540; JLCPCB Part # C17540
R13, R62: 200; R_0805_2012Metric_Pad1.20x1.40mm_HandSolder; MPN C17520; JLCPCB Part # C17540
R14, R25, R43: 2k2; R_0805_2012Metric_Pad1.20x1.40mm_HandSolder; MPN C17520; JLCPCB Part # C17520
R18, R19: 4k7; R_0805_2012Metric_Pad1.20x1.40mm_HandSolder; MPN C17540; JLCPCB Part # C17673
R21, R22, R23, R24, R27, R28, R29, R30: 300k; R_0805_2012Metric_Pad1.20x1.40mm_HandSolder; MPN C149504; JLCPCB Part # C17616
R26, R32: 1k; R_0805_2012Metric_Pad1.20x1.40mm_HandSolder; MPN C17513; JLCPCB Part # C17513
R31: 18k; R_0805_2012Metric_Pad1.20x1.40mm_HandSolder; MPN C4328; JLCPCB Part # C17506
R33: 0.01R; R_2512_6332Metric_Pad1.40x3.35mm_HandSolder; MPN C149504; JLCPCB Part # C241862
R34: 1k2; R_0805_2012Metric_Pad1.20x1.40mm_HandSolder; MPN C17379; JLCPCB Part # C17379
R36, R45, R52, R55, R58: 9k1; R_0805_2012Metric_Pad1.20x1.40mm_HandSolder; MPN C17414; JLCPCB Part # C17855
R37: 22k; R_0805_2012Metric_Pad1.20x1.40mm_HandSolder; MPN C17560; JLCPCB Part # C17560
R38: 51k; R_0805_2012Metric_Pad1.20x1.40mm_HandSolder; MPN C17737; JLCPCB Part # C17737
R40, R46: 82; R_0805_2012Metric_Pad1.20x1.40mm_HandSolder; MPN C17477; JLCPCB Part # C23255
R41, R47, R49, R54, R57, R60: 3k6; R_0805_2012Metric_Pad1.20x1.40mm_HandSolder; MPN C23255; JLCPCB Part # C18359
R48: 1k3; R_0805_2012Metric_Pad1.20x1.40mm_HandSolder; MPN C17414; JLCPCB Part # C17379
R50, R53, R56, R59: 82; R_0805_2012Metric_Pad1.20x1.40mm_HandSolder; MPN C23255; JLCPCB Part # C23255
R51: 47; R_0805_2012Metric_Pad1.20x1.40mm_HandSolder; MPN C23255; JLCPCB Part # C17714
R61: 9k1; R_0805_2012Metric_Pad1.20x1.40mm_HandSolder; MPN C23255; JLCPCB Part # C17855
R63: 10k; R_0805_2012Metric_Pad1.20x1.40mm_HandSolder; MPN C17540; JLCPCB Part # C17414
R64: 3.24k; R_0805_2012Metric_Pad1.20x1.40mm_HandSolder; MPN C17540; JLCPCB Part # C17609
R66: 330R; R_0805_2012Metric_Pad1.20x1.40mm_HandSolder; MPN C17630; JLCPCB Part # C17630
SW1, SW2, SW3, SW4: SW_MEC_5G; SW_Push_1P1T_XKB_TS-1187A; MPN C318884; JLCPCB Part # C318884
TP1, TP36, TP37: HIL_TSAL_HV_GND; TestPoint_Pad_D1.0mm; MPN DNP; JLCPCB Part # DNP
TP2: HIL_IN_TSAL; TestPoint_Pad_D1.0mm; MPN DNP; JLCPCB Part # DNP
TP3: DIS; TestPoint_Pad_D1.0mm; MPN DNP; JLCPCB Part # DNP
TP4: THR; TestPoint_Pad_D1.0mm; MPN DNP; JLCPCB Part # DNP
TP5, TP6, TP7, TP8, TP9, TP10, TP11, TP12, TP13, TP14, TP15, TP16, TP17, TP18, TP19, TP20, TP21, TP22, TP23, TP24, TP25, TP26, TP27, TP28, TP29, TP30, TP31, TP32, TP33, TP34, TP35, TP38, TP39, TP40: TestPoint_Pad_D1.0mm; MPN DNP; JLCPCB Part # DNP
U1, U5: SN65HVD230; SOIC-8_3.9x4.9mm_P1.27mm; MPN C12084; JLCPCB Part # C12084
U2: TMP101; SOT-23-6; MPN C388175; JLCPCB Part # C388175
U3: ESP32-WROOM-32; MPN C529581; JLCPCB Part # C529581
U4: STM32F446RETx; LQFP-64_10x10mm_P0.5mm; MPN C69336; JLCPCB Part # C69336
U6: MAX3232; TSSOP-16_4.4x5mm_P0.65mm; MPN C13482; JLCPCB Part # C13482
U7: TMR-1212; Converter_DCDC_TRACO_TMR-xxxx_THT; MPN DNP; JLCPCB Part # DNP
U8: MPU-6050; InvenSense_QFN-24_4x4mm_P0.5mm; MPN C24112; JLCPCB Part # C24112
U9: LM393; SOIC-8_3.9x4.9mm_P1.27mm; MPN C7955; JLCPCB Part # C7955
U10, U15, U17: LM358; SOIC-8_3.9x4.9mm_P1.27mm; MPN C7950; JLCPCB Part # C7950
U11: NE555DR; SOIC-8_3.9x4.9mm_P1.27mm; MPN C7593; JLCPCB Part # C7593
U12: EL357NC; SOP-4_3.8x4.1mm_P2.54mm; MPN C29981; JLCPCB Part # C29981
U13: DV24V150F12; D24V150F12; MPN DNP; JLCPCB Part # DNP
U14, U16: AMS1117-3.3; SOT-223-3_TabPin2; JLCPCB Part # C6186
U18: TPS5431DDA; TI_SO-PowerPAD-8_ThermalVias; JLCPCB Part # C9864
Y1: 9p; Crystal_SMD_3225-4Pin_3.2x2.5mm_HandSoldering; MPN C13738; JLCPCB Part # C13738
Y2: 12p5; Crystal_SMD_3215-2Pin_3.2x1.5mm; MPN C32346; JLCPCB Part # C32346

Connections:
+3.3VP: C2.1, C5.1, C6.1, C7.1, C8.1, C9.1, C10.1, C11.1, C13.1, C40.1, C46.1, C47.1, J4.1, R6.1, R62.1, SW2.1 (A), TP32.1, U1.3 (VCC), U4.1 (VBAT), U4.13 (VDDA), U4.19 (VDD), U4.32 (VDD), U4.48 (VDD), U4.64 (VDD), U5.3 (VCC), U16.2 (VO)
+3V3: C1.1, C3.1, C4.1, C14.1, C19.1, C25.1, C26.2, C36.1, C37.1, J2.4 (VDD), J5.1, R1.2, R2.2, R3.1, R4.2, R13.1, R18.2, R19.1, TP31.1, U2.4 (V+), U3.2 (VDD), U6.16 (VCC), U8.8 (VDDIO), U8.13 (VDD), U14.2 (VO)
+5V: C18.1, C39.1, C50.1, JP3.3 (B), JP4.3 (B), L1.1, R63.1, R66.1, TP33.1, TP38.1, U14.3 (VI), U16.3 (VI)
+12V: C30.2, C31.1, C38.1, C43.1, C48.1, J1.A2, J1.A4, J1.B4, J1.D4, J1.E1, J1.F2, J1.F3, J1.F4, J1.H4, J1.K4, J1.M1, J1.M2, JP3.1 (A), JP4.1 (A), JP7.1 (A), JP8.1 (A), R14.1, R25.1, R26.2, R32.1, R35.1, R43.1, TP39.1, U7.2 (+VIN), U10.8 (V+), U11.8 (VCC), U13.8 (VOUT), U15.8 (V+), U17.8 (V+), U18.7 (VIN)
/12V_BATTERY_IN: J1.M3, J1.M4, JP5.1 (A), JP6.1 (A), R33.2, R58.1
/12V_BATTERY_IN1: JP5.2 (B), JP6.2 (B), R33.1, R55.1, U13.1 (VIN)
/12V_INPUT_ADC1_IN0_Conn: JP7.3 (B), R36.1
/12V_INPUT_ADC1_IN1_Conn: JP8.3 (B), R45.1
/12V_INPUT_ADC1_IN3_Conn: J1.A1, R52.1
/ADC1_IN0: C32.1, R40.2, TP5.1, U4.14 (PA0)
/ADC1_IN1: C35.1, R46.2, TP6.1, U4.15 (PA1)
/ADC1_IN2: C41.1, R50.2, TP7.1, U4.16 (PA2)
/ADC1_IN3: C42.1, R53.2, TP9.1, U4.17 (PA3)
/ADC2_IN4: C44.1, R56.2, TP8.1, U4.22 (PA6)
/ADC2_IN5: C45.1, R59.2, TP10.1, U4.23 (PA7)
/BOOT0: R10.1, SW2.2 (B), U3.9 (IO33), U4.60 (BOOT0)
/BOOT0_F: J1.H2, U3.11 (IO26)
/Brake_Light_Conn: J1.C1, Q4.3 (D)
/Brake_Light_PA5: Q4.1 (G), R67.2, TP40.1, U4.21 (PA5)
/Buzzer_Conn: J1.F1, Q3.3 (D)
/Buzzer_PC6: Q3.1 (G), R65.2, TP25.1, U4.37 (PC6)
/CAN1_RX: TP13.1, U1.4 (R), U4.44 (PA11)
/CAN1_TX: TP14.1, U1.1 (D), U4.45 (PA12)
/CAN2H_N: D13.2 (K), J1.G3, JP2.2 (B), TP29.1, U5.6 (CANL)
/CAN2H_P: D13.1 (K), J1.H3, R12.2, TP28.1, U5.7 (CANH)
/CAN2_RX: TP12.1, U4.33 (PB12), U5.4 (R)
/CAN2_TX: TP11.1, U4.34 (PB13), U5.1 (D)
/CANH_N: D1.2 (K), J1.J1, JP1.2 (B), TP30.1, U1.6 (CANL)
/CANH_P: D1.1 (K), J1.K1, R5.2, U1.7 (CANH)
/COOLENT_TMEP_Conn: D9.1 (K), J1.B3, R51.2, U15.3 (+)
/DETECT_SDIO_INPUT: J2.10 (DET_A), R1.1, TP20.1, U4.56 (PB4)
/DIS: R26.1, R31.1, TP3.1, U11.7 (DIS)
/EXTI_2_PC5: J1.D1, U4.25 (PC5)
/GEN_B14: J1.C2, U4.35 (PB14)
/GEN_B15: J1.D2, U4.36 (PB15)
/GND_BATTERY_IN: J1.L3, J1.L4, U13.2 (GND)
/GREEN_LED_GND: J1.E2, Q6.3 (D)
/HV+: D3.2 (A), HV+1.1
/I2C1_SCL: R18.1, TP16.1, U2.1 (SCL), U4.61 (PB8), U8.23 (SCL)
/I2C1_SDA: R19.2, TP15.1, U2.6 (SDA), U4.62 (PB9), U8.24 (SDA)
/MOTOR_PUMP_1_SW: J1.J4, Q1.3 (D)
/MOTOR_PUMP_2_SW: J1.G4, Q2.3 (D)
/Motor_Pump_1_PC1: Q1.1 (G), R15.2, TP27.1, U4.9 (PC1)
/Motor_Pump_2_PC0: Q2.1 (G), R16.2, TP26.1, U4.8 (PC0)
/NRST: J4.5, R6.2, SW1.2 (B), U3.8 (IO32), U4.7 (NRST)
/NRST_F: J1.G2, U3.12 (IO27)
/OSC_RCC_32_IN: C23.1, U4.3 (PC14), Y2.1
/OSC_RCC_32_OUT: C24.1, U4.4 (PC15), Y2.2
/OSC_RCC_IN: C21.1, U4.5 (PH0), Y1.1
/OSC_RCC_OUT: C22.1, U4.6 (PH1), Y1.3
/PIN_B1: J1.B1, JP7.2 (C)
/PIN_B2: J1.B2, JP8.2 (C)
/PIN_K2: J1.K2, JP3.2 (C)
/PIN_K3: J1.K3, JP4.2 (C)
/RED_LED_GND: J1.E3, Q5.3 (D)
/SDIO_CK: J2.5 (CLK), TP18.1, U4.28 (PB2)
/SDIO_CMD: J2.3 (CMD), R4.1, TP17.1, U4.54 (PD2)
/SDIO_D0: J2.7 (DAT0), R2.1, TP19.1, U4.39 (PC8)
/SWCLK: J4.2, U4.49 (PA14)
/SWDIO: J4.4, U4.46 (PA13)
/SWO: J4.6, U4.55 (PB3)
/THR: C34.2, C52.2, R31.2, TP4.1, U11.2 (TR), U11.6 (THR)
/Tractive System Active: R49.2, R61.1, U4.53 (PC12)
/UART0_ESP_RX_STM: TP24.1, U3.28 (IO17), U6.12 (R1OUT)
/UART0_ESP_TX_STM: TP23.1, U3.27 (IO16), U6.11 (T1IN)
/UART1_RX_Conn: J1.G1, U6.13 (R1IN)
/UART1_STM_RX: J3.3, TP22.1, U3.37 (IO23), U4.43 (PA10)
/UART1_STM_TX: J3.2, TP21.1, U3.36 (IO22), U4.42 (PA9)
/UART1_TX_Conn: J1.H1, U6.14 (T1OUT)
/UART2_ESP_RX_USB: J5.4, U3.34 (RXD0/IO3)
/UART2_ESP_TX_USB: J5.3, U3.35 (TXD0/IO1)
GND: C1.2, C2.2, C3.2, C4.2, C5.2, C6.2, C7.2, C8.2, C9.2, C10.2, C11.2, C12.2, C13.2, C14.2, C17.2, C18.2, C19.2, C20.2, C21.2, C22.2, C23.2, C24.2, C25.2, C26.1, C27.2, C29.2, C30.1, C31.2, C32.2, C33.1, C34.1, C35.2, C36.2, C37.2, C38.2, C39.2, C40.2, C41.2, C42.2, C43.2, C44.2, C45.2, C46.2, C47.2, C48.2, C50.2, C51.1, C52.1, D1.3 (A), D2.1 (K), D6.2 (A), D7.2 (A), D9.2 (A), D10.2 (A), D11.2 (A), D12.2 (A), D13.3 (A), D14.1 (K), D15.1 (K), D16.1 (K), D17.1 (K), D18.2 (A), D19.1 (K), J1.A3, J1.C3, J1.C4, J1.D3, J1.E4, J1.J2, J1.J3, J1.L1, J1.L2, J2.6 (VSS), J2.9 (DET_B), J2.11 (SHIELD), J3.1, J4.3, J5.2, Q1.2 (S), Q2.2 (S), Q3.2 (S), Q4.2 (S), Q5.2 (S), Q6.2 (S), Q7.2 (S), Q8.2 (S), Q9.2 (S), R7.2, R8.1, R10.2, R11.2, R15.1, R16.1, R20.1, R41.1, R42.2, R47.1, R49.1, R51.1, R54.1, R57.1, R60.1, R64.2, R65.1, R67.1, SW1.1 (A), SW3.1 (A), SW4.2 (B), TP34.1, TP35.1, U1.2 (GND), U2.2 (GND), U3.1 (GND), U3.15 (GND), U3.38 (GND), U3.39 (GND), U4.12 (VSSA), U4.18 (VSS), U4.31 (VSS), U4.47 (VSS), U4.63 (VSS), U5.2 (GND), U6.15 (GND), U7.1 (-VIN), U8.1 (CLKIN), U8.11 (FSYNC), U8.18 (GND), U10.4 (V-), U11.1 (GND), U12.3, U13.5 (GND), U13.7 (GND), U14.1 (GND), U15.4 (V-), U16.1 (GND), U17.4 (V-), U18.6 (GND), U18.9 (GNDPAD), Y1.2, Y1.4
GNDPWR: C28.1, D5.2 (A), HV-1.1, R37.1, R48.1, TP1.1, U7.7 (-VOUT), U9.4 (V-), U12.2
unnamed: D2.2 (A), R9.2
unnamed: D3.1 (K), R21.2
unnamed: D4.2 (A), R25.2
unnamed: D4.1 (K), Q7.3 (D)
unnamed: D5.1 (K), R30.1, R38.2, TP2.1, U9.3 (+)
unnamed: D6.1 (K), R36.2, R41.2, U10.3 (+)
unnamed: D7.1 (K), R45.2, R47.2, U10.5 (+)
unnamed: D8.2 (A), R43.2
unnamed: D8.1 (K), Q9.3 (D)
unnamed: D10.1 (K), R52.2, R54.2, U15.5 (+)
unnamed: D11.1 (K), R55.2, R57.2, U17.3 (+)
unnamed: D12.1 (K), R58.2, R60.2, U17.5 (+)
unnamed: D14.2 (A), R13.2
unnamed: D15.2 (A), R62.2
unnamed: D16.2 (A), R14.2
unnamed: D17.2 (A), R17.2
unnamed: C49.2, D18.1 (K), L1.2, U18.8 (PH)
unnamed: D19.2 (A), R66.2
unnamed: JP1.1 (A), R5.1
unnamed: JP2.1 (A), R12.1
unnamed: Q5.1 (G), Q7.1 (G), R42.1, U11.3 (Q)
unnamed: Q6.1 (G), Q8.1 (G), Q9.1 (G), R35.2, R61.2, U12.4
unnamed: Q8.3 (D), R32.2, U11.4 (R)
unnamed: R21.1, R22.2
unnamed: R22.1, R23.2
unnamed: R23.1, R24.2
unnamed: R24.1, R27.2
unnamed: R27.1, R28.2
unnamed: R28.1, R29.2
unnamed: R29.1, R30.2
unnamed: R34.2, U9.1, U12.1
unnamed: R37.2, R38.1
unnamed: C51.2, R3.2, SW3.2 (B), U3.3 (EN)
unnamed: SW4.1 (A), U3.25 (IO0)
unnamed: TP36.1, TP37.1
unnamed: R7.1, U1.8 (Rs)
unnamed: R8.2, U2.5 (ADD0)
unnamed: R9.1, U3.16 (IO13)
unnamed: R17.1, U4.29 (PB10)
unnamed: C12.1, U4.30 (VCAP_1)
unnamed: R11.1, U5.8 (Rs)
unnamed: C15.1, U6.1 (C1+)
unnamed: C15.2, U6.3 (C1-)
unnamed: C16.2, U6.4 (C2+)
unnamed: C16.1, U6.5 (C2-)
unnamed: C17.1, U6.2 (VS+)
unnamed: C20.1, U6.6 (VS-)
unnamed: R20.2, U8.9 (AD0)
unnamed: C27.1, U8.20 (CPOUT)
unnamed: C29.1, U8.10 (REGOUT)
unnamed: R44.1, R48.2, U9.2 (-)
unnamed: R40.1, U10.1, U10.2 (-)
unnamed: R46.1, U10.6 (-), U10.7
unnamed: C33.2, U11.5 (CV)
unnamed: R50.1, U15.1, U15.2 (-)
unnamed: R53.1, U15.6 (-), U15.7
unnamed: R56.1, U17.1, U17.2 (-)
unnamed: R59.1, U17.6 (-), U17.7
unnamed: C49.1, U18.1 (BOOT)
unnamed: R63.2, R64.1, U18.4 (VSENSE)
VDD: C28.2, R34.1, R44.2, U7.6 (+VOUT), U9.8 (V+)

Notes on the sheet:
DRIVER OUTPUT
IMU SENSOR
SECONDARY 5V BUCK
LOW VOLTAGE BATTERY MONITORING
Connector Interlock
MOUNTING HOLES
PRIMARY CONNECTOR
TRACTIVE SYSTEM ACTIVE LIGHT
ANALOG INPUTS
CAN PHYSICAL
CRYSTALS
STM32F446RE
STM UART CONNECTION
POWER DISTRIBUTION
UART DRIVER
ESP32-WROOM
SWD CONNECTION
TEMP SENSOR
SDIO 1-BIT



Board: 4 copper layers, 155.3 x 110.2 mm, 266 parts (22 on the bottom side), 134 nets.

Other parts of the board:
kibuzzard-662AAFE3: G***; kibuzzard-662AAFE3
kibuzzard-662AAFFB: G***; kibuzzard-662AAFFB
kibuzzard-662AB0CA, kibuzzard-662AB0CA#2: G***; kibuzzard-662AB0CA
kibuzzard-662AB0E0: G***; kibuzzard-662AB0E0
kibuzzard-662AB0FB: G***; kibuzzard-662AB0FB
kibuzzard-662AB2BE: G***; kibuzzard-662AB2BE
kibuzzard-662AB2D6: G***; kibuzzard-662AB2D6
kibuzzard-662AB3ED, kibuzzard-662AB3ED#2: G***; kibuzzard-662AB3ED
kibuzzard-662AB6B1: G***; kibuzzard-662AB6B1
kibuzzard-662AB6C8: G***; kibuzzard-662AB6C8
kibuzzard-662AB33B: G***; kibuzzard-662AB33B
kibuzzard-662AB64B: G***; kibuzzard-662AB64B
kibuzzard-662AB66E: G***; kibuzzard-662AB66E
kibuzzard-662AB70F: G***; kibuzzard-662AB70F
kibuzzard-662AB83B: G***; kibuzzard-662AB83B
kibuzzard-662AB099: G***; kibuzzard-662AB099
kibuzzard-662AB133: G***; kibuzzard-662AB133
kibuzzard-662AB341: G***; kibuzzard-662AB341
kibuzzard-662AB351: G***; kibuzzard-662AB351
kibuzzard-662AB427: G***; kibuzzard-662AB427
kibuzzard-662AB489: G***; kibuzzard-662AB489
kibuzzard-662AB611: G***; kibuzzard-662AB611
kibuzzard-662AB700: G***; kibuzzard-662AB700
kibuzzard-662AB830, kibuzzard-662AB830#2: G***; kibuzzard-662AB830
kibuzzard-662AB884: G***; kibuzzard-662AB884
kibuzzard-662C04C8: G***; kibuzzard-662C04C8
kibuzzard-662C048A: G***; kibuzzard-662C048A
kibuzzard-662C051A: G***; kibuzzard-662C051A
kibuzzard-662C063D: G***; kibuzzard-662C063D
kibuzzard-662C0490: G***; kibuzzard-662C0490
kibuzzard-662C0496: G***; kibuzzard-662C0496
kibuzzard-662C0665: G***; kibuzzard-662C0665
kibuzzard-662C0670: G***; kibuzzard-662C0670
